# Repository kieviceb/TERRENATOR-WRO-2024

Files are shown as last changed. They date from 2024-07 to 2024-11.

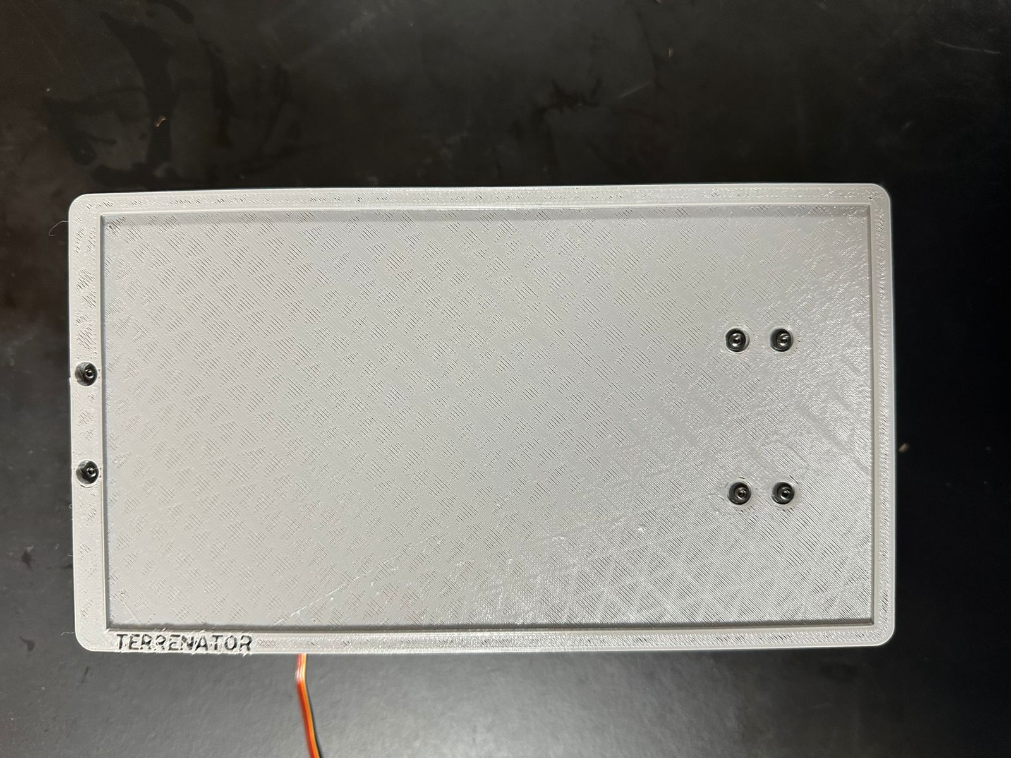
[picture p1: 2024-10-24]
v-photos/WhatsApp Image 2024-10-24 at 6.23.05 AM.jpeg

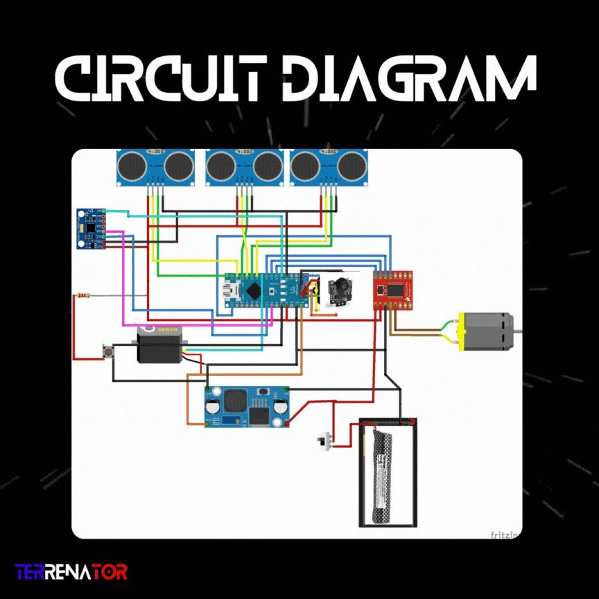
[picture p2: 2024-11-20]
Schemes/Circuit Diagram.jpg

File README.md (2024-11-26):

# Terrenator's readme Bandera de Panamá
TERRENATOR (30 x 18 cm) (25 x 6 cm) (1)



                
This is the official repository of the TERRENATOR team, which is representing Panama in the World Robotics Olympics (WRO) 2024 to be held this year in Izmir, Türkiye. We chose to participate in the category of Future Engineers this year winning first place in the national robotics olympics in our country. In this repository you can find everything related to the development of our robot.

---

## Team members 👨‍💻

Imagen 1

 ## David Rico:
 ### Age: 17

 Imagen 1
 
 David is someone who always tries to solve and constantly seeks the union in the team, he likes sports specifically baseball and likes anime and likes to win.

His role in the team is to design the chassis and 3d parts of the robot, also the circuit and all the components of the robot as well as programming.

## Ericka Ceballos:
### Age: 17

Imagen 1

She is very determined and strong, she is always very tidy and organized and above all she doesn't like to lose, ericka likes programming especially in python, she also likes to socialize a lot, as she is the sociable member of the team.

Her role in the team is the programming of the robot, as well as documenting the whole process of the robot.

## Jean Paul Sosa:
### Age: 17

 Imagen 1

He is the quietest of the team, but at the same time he always likes to be neutral in everything, he is someone that you will hardly make him angry, he is a quiet, chill guy. He loves music and enjoys listening to rock and playing instruments like the guitar, bass and saxo, as well as robotics.

His role in the team is to do some of the robot programming as well as help with the circuitry and documenting everything on the robot.

<br>
 <br>

 > [!NOTE]
> To see the funny photo [here](https://github.com/kieviceb/TERRENATOR-WRO-2024/tree/main/t-photos)

<br>

## Overview of our repository 📜
* `schemes`- contains the circuit diagram.
* `models` - includes all the 3d printed parts of the robot that will go to the international.
* `old models` - includes all the 3d printed parts of the robot that wins in Panama.
* `others`-  This is for other files which can be used to understand the making of the vehicle. 
* `src` - the codes for both challenges, with and without obstacles.
* `t-photos` - photos of the team one formal and a funny one.
* `v-photos` - photos of every angle of the robot, including our previuos version .
* `video` - the link to our youtube channel where you can see our robot in action completing both challenges.
* `README.md` - Here's all our journey in the development of our robot here we explain every part of the robot making.

## Components 🧱
A list of all the electrical and mechanical components in the robot.

|  |  |  | 
| :---: |:---:| :---:|
|[Arduino NANO A000005 x1](https://store-usa.arduino.cc/products/arduino-nano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)|[MPU6050 Gyroscope x1](https://a.co/d/42jYlB6)|[Step down LM2596 x1](https://a.co/d/e4jJKCS)|
|  |  |  |
| [Double Sided Prototype Universal PCB Board x2](https://a.co/d/9mUTqVe) |[TB6612 motor driver](https://a.co/d/fpJSHg1)|[HC-SRO4 ultrasonic sensor x3](https://a.co/d/et6RN4v) |
|  ||  |
|[POLOLU Metal Gearmotor 25Dx65L mm MP 12V with 48 CPR Encoder x1](https://www.pololu.com/product/4863)|[INJORA 7KG 2065 micro servo motor x1](https://a.co/d/3OIRFif)|[Tosiicop Airsoft Lipo Battery 11.1V x1](https://a.co/d/4mkS5gP)|
|  |  |  |
|[Pixy cam v2.1 x1](https://a.co/d/hyOCC5F) |[Electrolytic Capacitor x2](https://a.co/d/2Hp40r2)|[Rocker switch x1](https://a.co/d/dZaNOAK) |
|  |  |  |
|[10K ohm Resistor x1](https://a.co/d/g2p8k1C) |[UTP cable CAT6 ](https://a.co/d/9NCzytp)|[Push button x1](https://a.co/d/8YSMDxr) |
|  |  |  |
|[Fuse Holder Inline screw type x1](https://a.co/d/7VGbSVK) |[Jumper wires x12 ](https://a.co/d/0rLEQiV)|[Ceramic capacitor x3](https://amzn.eu/d/0qPpxa0) |

## Introduction 🎓

- To make all the structure of the robot, it took a lot of time and investigation, we decided to build our robot totally by our selves, the robot's body was make in [OnShape](https://www.onshape.com/en/) Platform , all the design of the robot and all the models and pieces can be found here in `models`, it is compound by 17 parts assembled together. We have passed by a lot of prototypes, at first heavier and bigger, but for turkiye prototype, to make it more light, more smaller, more efficient, we are looking to make the things simple, to make the most efficient autonomous vehicle, we decided to use [Arduino Nano](https://store.arduino.cc/products/arduino-nano) , because it's smaller and has everything that we need to control our robot, we have use a various types of Arduino nano, Like the [Arduino Nano ESP32](https://store.arduino.cc/products/nano-esp32), [Arduino Nano Every](https://store.arduino.cc/products/arduino-nano-every), [Arduino Nano Every](https://store.arduino.cc/products/arduino-nano-every). The reason of why we have used various types of arduino nano, is because every one of them give different capacities, and sometimes we need different capacities in our robot. To understand the making and the programming of the robot please check all the parts of this `README.md`.

## Vehicle Photos 📸

| Front | Right | Back |
|:---:|:---:|:---:|
| front |front |  front |
| Left | Top | Bottom |
|front| front | front|

<br>
 <br>

 > [!NOTE]
>These photos are of the vehicle that will travel to Turkiye to participate in WRO 2024, to see the photos of the car that won the robotics olympics in Panama you can go to the photos folder of the vehicle by clicking [here](https://github.com/kieviceb/TERRENATOR-WRO-2024/tree/main/v-photos)

<br>

---

## Circuit Diagram

<p align="center">
  Imagen 1
</p>

This circuit diagram represents the connections of a robotic system powered by a battery pack and controlled by an Arduino Nano. It integrates three ultrasonic sensors for obstacle detection, a servo motor for steering, and a DC motor for torque and speed via a TB6612 motor driver module. The MPU6050 sensor provides orientation data (gyroscope and accelerometer), likely used for navigation adjustments. A Pixy Cam is included for visual object tracking. Connections include multiple power and ground lines to ensure stable operation, while the battery supplies energy to the motors and sensors. UTP wires link the Arduino to the motor driver, servo, and sensors, ensuring precise control and data flow.

<br>
 <br>

 > [!NOTE]
> To a more detailed explanation go to the schemes readme by clicking [here](https://github.com/kieviceb/TERRENATOR-WRO-2024/tree/main/Schemes)

<br>

---

## Mobility Strategy 🚲

### 1- Movement

- Motor: Our  gearmotor consists of a medium-power, 12 V brushed DC motor combined with a 20.4:1 metal spur gearbox, and it has an integrated 48 CPR quadrature encoder on the motor shaft, which provides 979.62 counts per revolution of the gearbox’s output shaft. The gearmotor is cylindrical, with a diameter just under 25 mm, and the D-shaped output shaft is 4 mm in diameter and extends 12.5 mm from the face plate of the gearbox, you can find our motor [here](https://www.pololu.com/product/4863).

<p align="center">
  Imagen 1
</p>

We used a 3D printed traction system in the back axle of the car, is specifically designed to enhance performance and maneuverability. This system involves a set of precisely engineered gears that provide consistent and reliable power transfer from the motor to the rear wheels. The gear configuration ensures that torque is effectively distributed, enabling the car to maintain traction even during rapid acceleration. It provides the power, control, and reliability needed for the commpetition.

### 2- Steering
 
- Steering: The steering is handled by a servomotor, during this project we discovered that using a plastic gear servo is not a good choice, because of the speed of the robot, it tends to break easily inside; thats how we ended up using at first a MG995 servo which is metal gear so it doesnt break so easily, finally for the last prototype to reduce weight and size we found a micro metal gear servo (INJORA 7KG 2065 micro servo motor) , with the power of the big one but weighting less and smaller. Having the steering on the front axle, in vertical position to make movement with more precission.  

<p align="center">
  Imagen 1
  Imagen 2
</p>

### 3- Sensors

- [HC-SR04](https://www.sparkfun.com/products/15569):
The HC-SR04 is a distance sensor that uses ultrasound to determine the distance of an object in a range of 2 to 450 cm. It is notable for its small size, low power consumption and good accuracy. The HC-SR04 sensor is the most widely used ultrasonic sensor, mainly due to the amount of information and projects available on the web. It is also the most used in robotics projects such as maze or sumo robots, and in automation projects such as level or distance measurement systems.

This sensor provides 2cm to 400cm of non-contact measurement functionality with a ranging accuracy that can reach up to 3mm. Each HC-SR04 module includes an ultrasonic transmitter, a receiver and a control circuit.

<p align="center">
  Imagen 1
</p>

-How the HC-SR04 Ultrasonic Distance Sensor Works?
It emits an ultrasound at 40 000 Hz which travels through the air and if there is an object or obstacle on its path It will bounce back to the module. Considering the travel time and the speed of the sound you can calculate the distance.

<p align="center">
AJAJ
</p>

In order to generate the ultrasound we need to set the Trig pin on a High State for 10 µs. That will send out an 8 cycle ultrasonic burst which will travel at the speed of sound. The Echo pins goes high right away after that 8 cycle ultrasonic burst is sent, and it starts listening or waiting for that wave to be reflected from an object.

To detect the walls with the HC-SR04 it took us a lot of time to figure out a way of using the ultrasonic sensors to avoid the walls successfully, in our previous prototype we had all the sensors horizontally and it gave us good lectures most of the time, but not always, thats why investigating a little further and using trigonometry we found out that the position of the ultrasonic sensors on the sides vertically is way more effective and the main reason we were having trouble at the curves; What was happening was that the TX and RX sides, when reaching the curves, one was further ahead than the other and the pulse did not reach the same place and was sending out erroneous data, therefore when placing them vertically this does not happen, both pulses collide equally, and the signal bounces back uniformly, sending out useful data.

<p align="center">
Imagen 1
</p> 

In addition to this, as can be seen in the photos of the vehicle, our ultrasonic sensors each have a Ceramic capacitor, and before explaining why we have it we should know what it is. A ceramic capacitor is a fixed-value capacitor where the ceramic material acts as the dielectric. It is formed by two or more alternating layers of ceramic and a metallic layer that acts as the electrode. The composition of the ceramic material defines the electrical behavior and therefore the applications.

Knowing this, our intention in placing these ceramic lentils or capacitors is to be able to soften the signals of the ultrasonic sensors, so to speak, filter the signals; this helped to not protrude peaks in the sound waves transmitted by the ultrasonic sensor and so that all data are received with the greatest possible clarity.

<p align="center">
Imagen 1
</p> 

- [MPU-6050](https://invensense.tdk.com/products/motion-tracking/6-axis/mpu-6050/):
MPU6050 sensor module is complete 6-axis Motion Tracking Device. It combines 3-axis Gyroscope, 3-axis Accelerometer and Digital Motion Processor all in small package. Also, it has additional feature of on-chip Temperature sensor. It has I2C bus interface to communicate with the microcontrollers. It has Auxiliary I2C bus to communicate with other sensor devices like 3-axis Magnetometer, Pressure sensor etc. If 3-axis Magnetometer is connected to auxiliary I2C bus, then MPU6050 can provide complete 9-axis Motion Fusion output.
<p align="center">
Imagen 1
</p> 

- Orientation and polarity of the axes and rotations of the MPU-6050:
It is a 6-axis motion sensor that measures linear accelerations and angular velocities. It uses a three-dimensional coordinate system with axes labeled +X, +Y and +Z, representing forward/backward, left/right and up/down directions, respectively. The +X axis points to the right, +Y points up and +Z points vertically away from the top surface of the sensor, with their negative counterparts in the opposite directions. Rotational motions are measured around these axes, with positive rotation defined by the right-hand rule: if the fingers of the right hand are bent in the direction of rotation, the thumb points along the positive axis. For example, clockwise rotation around the +X (roll), +Y (pitch) or +Z (yaw) axes is considered positive, while counterclockwise rotation is negative. This configuration allows the MPU-6050 to track motion in 3D, making it essential for applications such as balancing robots, drones or any system that requires accurate tracking of motion and orientation.
<p align="center">
Imagen 1
</p> 
For our vehicle, we are only interested in the z-axis (Yaw) of the MPU-6050, because this axis is the one that will allow us to determine the desired angles for our robot to work, in our vehicle, we have to let the sensor calibrate to start, at the time of being calibrated the angles that we are interested in are those of 90 degrees to be able to make a right angle turn and to help stabilize the PD, we had an issue that in the straight lines the PD is well stabilized, but when making the curves it went crazy, and began to oscillate a lot, then to have more precise turns, We used the Z axis (Yaw) of the MPU-6050, but this also had its complications, because the values sent by the z axis were not so simple for the robot to understand, because the first curve, if they were 90 degrees, but the next curve for example the gyroscope threw 180 degrees, and it is logical, but it was more difficult to implement, so we thought of several possible solutions for this, we thought of resetting the values of Yaw or the z-axis after each curve, so that if in the serial we can always see that it turns 90 degrees exactly, this greatly affected the accuracy of the sensor.

 <br>
 <br>

 > [!NOTE]
>In order to see the coding of each motion component or sensor explained, please go to the coding part for further understanding, as well as you can always review the vehicle circuit diagram and review the component list, and also you can check our youtube channel. [Here](https://www.youtube.com/@TERRENATORTEAM)

<br>
In this way, in the vehicle, the MPU-6050 works using the desired angles through functions so that the robot can make precise turns. I will go into much more detail about this in the code section.

### 4- [MPU-6050 LIBRARIES](https://invensense.tdk.com/products/motion-tracking/6-axis/mpu-6050/):

 First of all we need to initialize our MPU-6050 We need to declare all the variables for it, and it has some specific libraries that you can find it here:

https://github.com/jrowberg/i2cdevlib
https://github.com/ZHomeSlice/Simple_MPU6050
https://github.com/ZHomeSlice/Simple_Wire

And if you don't know how to install it, you need to watch this video, (it's in spanish):

- [MPU-6050  Youtube](https://www.youtube.com/watch?v=TwFZ4BJUX5c&t=1805s)

But i´ll explain here:
First we need to donwload the I2C Library that will make easy the 12c conection with the arduino nano, this library it´s of free software and multiplatform, and this library complement the wire library with the arduino IDE, so, we need to goon the first link i put here and [here](https://github.com/jrowberg/i2cdevlib) then, in the part of code, the green part on the git hub, we will donwnload the zip, so once it is installed we need to extract the file, once it is extracted, we need to go to the 12cdevlib master folder, then the arduino folder, here are a lot of libraries we can use for different proyects, so here we have to search the 12cdev folder, once we find it we have to select it an copy it, so once we do this we have to go to arduino folder, in most of cases it is set default on document, once there we go to libraries and then we paste 12cdev there.

That was our first library, now we need to download the [Simple_MPU6050](https://github.com/ZHomeSlice/Simple_MPU6050)  library, wich this is most simple to use, so we have to intall the zip of this library, and then in the arduino IDE we have to include the library there, in other words we have to add the zip file to his library inside the IDE.

Even in this part you might have some problems to initialize and use the code, that´s because in the video they dont say this but we need another library, that is for comunication, espacifically the [Simple_Wire](https://github.com/ZHomeSlice/Simple_Wire), to install it you have to follow the same steps of the second library.

Once we have all the libraries needed, we are ready to use the MPU-6050.

### 4- Camera

- 5-[PIXY CAM 2.1](https://pixycam.com/2021/05/20/introducing-pixy-2-1/):
The PixyCam 2.1 is a fast and versatile vision sensor for DIY robotics, offering significant improvements over its predecessor. Its horizontal field-of-view has been expanded to 80 degrees, allowing it to capture more of the environment in each frame, albeit with minor spherical distortion. The camera features a replaceable M12 lens mount with adjustable focus, enabling it to focus on objects as close as 0.25 inches. It also minimizes chromatic distortion at the edges and boasts an F-stop of 2.0, improving light gathering and reducing pixel noise, resulting in higher detection accuracy. Capable of processing images at 60 frames per second, it updates object positions every 16.7 milliseconds, making it ideal for tracking fast-moving objects or precise line-following. The Color Connected Components (CCC) algorithm allows to detect objects based on hue and saturation, remaining robust under varying lighting conditions. It supports up to 7 color signatures or numerous objects using color codes. While retaining the software, firmware, and features of PixyCam 2, this version is slightly larger but significantly more efficient for detection and tracking tasks.
---
<p align="center">
  Imagen 1
  Imagen 2
</p>

<br>
 <br>
 
---

 > [!NOTE]
>In the case of our pixy cam 2.1, we always need to calibrate our camera before the competition in the track of the event, this because as it has happened to us before we always need to check that the pixy cam recognizes well the blocks and the color lines, because it happens that the illumination affects the block detection of the pixy cam, then we always need to enter the track with our laptop using specifically the pixymon program, to be able to know that the signatures are being detected effectively, to calibrate our pixy cam we need to use a microUSB cable connected to the laptop to open the pixymon, pixymon is to check the view of the camera.

<br>

## Chasis & 3D Parts

In the chassis and 3D part, you can find all the 3D parts that made up the robot that won in Panama in the old models part.

So the chassis and the design of the car going to Turkey took a long time because our ideas; to make the robot of the national competition much smaller, agile, faster and prettier, we had to make a completely new chassis, in this one changing several parts of the assembly, for example in the steering system, since in our previous robot, the steering system was based on moving a cylinder with teeth that moved a stripped line that gave direction to the robot, the problem with this steering design was that its a bit imprecise so, we adopted a steering design similar to the Ackerman steering, and we also changed the servo motor.

---
<p align="center">
  Imagen 1
  Imagen 2
</p>
---

Then for the traction, we have four parts, the big gear for motor that this is the gear that give us the torque to move the robot, we have a game of gears that we can modify in case we need speed or more torque, and we have a fixed drive motor retainer, here we have a support for the motor, and we have the small gear for the drive axle, and we have the traction support.

---
<p align="center">
  Imagen 1
  Imagen 2
</p>

---
Then we have the skeleton: 
Here in the skeleton is the main base chasis of the robot, here we can find in the physical one the motor game with his gears, the servo motor, and the modifications that make the steering have better movements.

And also here we have the main shell, here we can find all that makes our robot, here are all the circuits for the robot and the base for the camera.

---
<p align="center">
  Imagen 1
  Imagen 2
</p>

---

Now for the sensors, we have made a lot of support for them, but with this one we made the correct one, it is more outside beacuase they give us better data in this way.

---

<p align="center">
  Imagen 1
</p>

---

Now with the wheels, we have designed it by ourself, because in that way we can ajust everything we want and it's so much better in that way. For the traction wheels they are a little bit bigger.

---
<p align="center">
  Imagen 1
  Imagen 1
</p>

<br>
 <br>

 > [!NOTE]
> All this can be find in the main [README](https://github.com/kieviceb/TERRENATOR-WRO-2024/blob/main/README.md) And very important you can see a tutorial video of all the structure of the robot by clicking [here](https://www.youtube.com/@TERRENATORTEAM)

<br>

## Code & programming
In this section, we will proceed to explain the codes of the open and obstacle challenge, the codes will be explained SEQUENTIALLY in the SRC folder, there you will have a more general explanation of the code, in this part of the readme we will break down the code of each component that integrates the code, to have a much clearer and understandable epxlicacion each part of the code. Before going to explain each code of the respective round, there will be a list to know the order in which each part of the code will be explained, and remember to see the sequential explanation, it is in the SRC folder.

## Open Challenge Code:

### 1. **Library Imports**

```ino
#include <Servo.h>
#include "Simple_MPU6050.h"
#include <Wire.h>
```
- **Servo.h**: Used to control a servo motor.
- **Simple_MPU6050.h**: Library for interfacing with the MPU6050 sensor (used for orientation).
- **Wire.h**: Library for I2C communication, necessary for interacting with the MPU6050.

---

### 2. **MPU6050 Configuration**
```ino
#define MPU6050_ADDRESS_AD0_LOW     0x68   // I2C address when AD0 pin is LOW
#define MPU6050_ADDRESS_AD0_HIGH    0x69   // I2C address when AD0 pin is HIGH
#define MPU6050_DEFAULT_ADDRESS     MPU6050_ADDRESS_AD0_LOW  // Default I2C address for the MPU6050

Simple_MPU6050 mpu;  // Create an instance of the MPU6050 object
float yawActual = 0;  // Global variable to store the current Yaw (rotation around the Z-axis)
float yawInicial = 0; // Initial yaw value for reference
```
- Defines the I2C addresses for the MPU6050 sensor, depending on the state of the AD0 pin.
- Initializes the `Simple_MPU6050` object for reading data from the sensor.
- `yawActual` holds the current yaw angle (rotation around the Z-axis).
- `yawInicial` stores the initial yaw value, often used for calculating differences in orientation.

---

### 3. **Servo configuration**
```ino
Servo servoDireccion;  // Servo object to control the steering
int pinServo = 6;      // Pin to which the servo is connected
int anguloIzquierda = 87;  // Angle for left turn
int anguloCentro = 90;      // Angle for straight position (centered)
int anguloDerecha = 105;    // Angle for right turn
int anguloMPU = 0;         // Angle value derived from MPU data
```
Initializes the servo and assigns specific angles for left, center, and right turns; also a derivated angle from the mpu6050.

### 4. **PD Control (Proportional-Derivative Control) Variables**
Before we explain the coding of this, we need to explain what is it:

PD Control (Proportional-Derivative) is a technique in control theory used to adjust the behavior of a system based on:

-The current error (Proportional): How much the system deviates from the desired value at this moment.
-The rate of change of the error (Derivative): How quickly the error is changing over time.

A PD controller is a simplified form of the PID control, omitting the Integral term. It is useful when:

-Accumulated errors (integral term) do not need to be eliminated.
-The system requires fast and stable responses.

Mathematical Function of PD
The output of the controller (referred to as adjustment or correction) is calculated as:
null-109

where Kp is the proportional gain, Kd the derivative gain, the error the difference between the desired value (setpoint) and the current system value and and d multiplied by the error between d its the Derivative of the error, i.e., the rate of change of the error over time.

-Implementation of PD Control in the code:
The code uses a PD controller to dynamically adjust the servo motor angle based on error. Below, I break down each step of its implementation:

float Kp = 2.0;: Defines the proportional gain.

A higher value means that the system responds more aggressively to error.
Too high a value can make the system unstable (oscillate).
float Kd = 1.0;: Defines the derivative gain.

Helps to smooth the system response. If the error is changing rapidly, this term reduces the setting to avoid oscillations.
float lastError = 0;: Variable to store the error of the previous iteration.
```ino
float Kp = 0.63;  // Proportional gain for PD control
float Kd = 0.4;   // Derivative gain for PD control
float alpha = 0.15;  // Smoothing factor for yaw
float lastError = 0; // Stores the last error value for derivative calculation
int curva = 0;      // Counter for curves detected by the robot
const int botonPin = A7;  // Button pin used to start/stop the robot
bool enMarcha = false;    // Robot's state: false = stopped, true = running
```
- **PD control constants** (`Kp` and `Kd`): Used to tune the proportional and derivative responses of the control loop.
- **Yaw smoothing** (`alpha`): A factor used to smooth the yaw (orientation) readings from the MPU6050 to avoid abrupt changes.
- **Button and robot state**: The button on pin `A7` is used to start or stop the robot. `enMarcha` indicates whether the robot is running or stopped.

---

### 5. **Ultrasonic Sensor and MotorPin Setup**

```ino
int trigIzquierdo = 9, echoIzquierdo = 10;  // Left sensor pins
int trigCentro = 15, echoCentro = 14;        // Center sensor pins
int trigDerecho = 7, echoDerecho = 8;        // Right sensor pins

int motorPin1 = 5, motorPin2 = 4, enablePin = 3, standbyPin = 16;  // Motor pins for control
```
- Defines the pins for the three ultrasonic sensors (left, center, right). These are used to detect obstacles.
- Motor control pins: These pins are used to control the motors (direction, enable, and standby).

---

### 6. **Time Control and Blocking Variables**

```ino
unsigned long tiempoUltimaCurva = 0;
const long bloqueoTiempo = 2000;  // Time between turns to avoid continuous turning
int bloqueadorI = 65;  // Blocking threshold for left sensor
int bloqueadorD = 65;  // Blocking threshold for right sensor
```
- `tiempoUltimaCurva`: Stores the last time a curve was detected to prevent rapid consecutive curve turns.
- `bloqueoTiempo`: Time interval (in milliseconds) that defines how often the robot can turn to avoid constant turns.
- `bloqueadorI` and `bloqueadorD`: Thresholds for the left and right sensors to prevent false readings from triggering unnecessary turns.

---

### 7. **MPU6050 Data Processing Function**

```ino
void procesarMPU(int16_t *gyro, int16_t *accel, int32_t *quat, uint32_t *timestamp) {
    Quaternion q;  // Quaternion object to store rotation data
    VectorFloat gravity;  // Gravity vector for accurate yaw calculation
    float ypr[3] = { 0, 0, 0 };  // Yaw, pitch, roll values
    float xyz[3] = { 0, 0, 0 };  // Raw sensor data values

    // Get quaternion, gravity, and yaw-pitch-roll data from the MPU
    mpu.GetQuaternion(&q, quat);
    mpu.GetGravity(&gravity, &q);
    mpu.GetYawPitchRoll(ypr, &q, &gravity);
    mpu.ConvertToDegrees(ypr, xyz);

    // Update the yaw value globally
    yawActual = (int)xyz[0];
}
```
- **`procesarMPU`**: This function processes the MPU6050 data (gyroscope, accelerometer) to extract yaw, pitch, and roll values using quaternions and gravity data. The yaw value (`yawActual`) is updated globally.

---

### 8. **PD Control Initialization**

```ino
void inicializarControlPD() {
    servoDireccion.attach(pinServo);  // Attach the servo to the pin
    //servoDireccion.write(anguloCentro); // Optional: Set the servo to the center position (straight)
}
```
- **`inicializarControlPD`**: Initializes the PD control by attaching the servo to the specified pin and optionally setting it to the center position.

---

### 9. **Servo Control Function**

```ino
void move_steer(int pos) {
    int currentPos = servoDireccion.read();  // Get the current position of the servo
    if (pos > currentPos) {
        // Move the servo to the right (gradually increasing position)
        for (int i = currentPos; i <= pos; i++) {
            servoDireccion.write(i);
            delay(10);  // Small delay to smooth the movement
        }
    } else {
        // Move the servo to the left (gradually decreasing position)
        for (int i = currentPos; i >= pos; i--) {
            servoDireccion.write(i);
            delay(10);  // Small delay to smooth the movement
        }
    }
}
```
- **`move_steer`**: This function smoothly moves the servo to a target position (`pos`). It adjusts the servo's position incrementally (with small delays) to avoid abrupt movements.

### 10. **PD Control Adjustment Function**

```ino
void ajustarAngulo(float error, int anguloDeseado) {
    float derivada = error - lastError;  // Calculate the derivative term (rate of change of error)
    float ajuste = (Kp * error) + (Kd * derivada);  // PD control formula
    lastError = error;  // Update the last error value for the next iteration

    anguloDeseado += ajuste;  // Apply the adjustment to the desired angle
    anguloDeseado = constrain(anguloDeseado, anguloIzquierda, anguloDerecha);  // Constrain the angle to avoid exceeding limits
    move_steer(anguloDeseado);  // Move the servo to the adjusted angle
}
```
- **`ajustarAngulo`**: This function adjusts the steering angle based on the error (difference between desired and actual angles) using the PD control formula. It ensures the angle stays within limits (`anguloIzquierda` and `anguloDerecha`) and moves the servo accordingly.

---
### 11. **Ultrasonic Sensor Distance Measurement**

```ino
long medirDistancia(int trigPin, int echoPin) {
    // Trigger the ultrasonic sensor
    digitalWrite(trigPin, LOW);  // Start with LOW to ensure a clean pulse
    delayMicroseconds(3);
    digitalWrite(trigPin, HIGH);  // Send a HIGH pulse to trigger the sensor
    delayMicroseconds(10);
    digitalWrite(trigPin, LOW);  // End the pulse

    // Measure the duration of the echo pulse
    long duracion = pulseIn(echoPin, HIGH);  // Get the duration of the echo signal
    return duracion * 0.034 / 2;  // Convert the duration into distance (in cm)
}
```
- **`medirDistancia`**: This function triggers the ultrasonic sensor and calculates the distance based on the time it takes for the echo to return.

---

### 12. **Function: `calcularAnguloObjetivoI(int curva)`**

```ino
int calcularAnguloObjetivoI(int curva) {
    if (curva % 4 == 1) return -70;     // Curvas 1, 5, 9, ...
    else if (curva % 4 == 2) return -160; // Curvas 2, 6, 10, ...
    else if (curva % 4 == 3) return 110;   // Curvas 3, 7, 11, ...
    else return 20;                      // Curvas 4, 8, 12, ...
}
```

This function calculates the target angle for the servo motor (or steering mechanism) based on the curve number. The variable `curva` represents the current curve number.
- The function uses the modulo operator (`%`) to determine the remainder when dividing `curva` by 4. This helps categorize the curve into one of four possible cases (1 through 4).
- Based on the result of the modulo operation, the function returns a specific angle for the servo.
Here’s how the curve number determines the angle:
- **When `curva % 4 == 1`** (i.e., curves 1, 5, 9, ...): The servo will turn to **-70°**.
- **When `curva % 4 == 2`** (i.e., curves 2, 6, 10, ...): The servo will turn to **-160°**.
- **When `curva % 4 == 3`** (i.e., curves 3, 7, 11, ...): The servo will turn to **110°**.
- **When `curva % 4 == 0`** (i.e., curves 4, 8, 12, ...): The servo will turn to **20°**.

### 13. **Function: `calcularAnguloObjetivoD(int curva)`**

```ino
int calcularAnguloObjetivoD(int curva) {
    if (curva % 4 == 1) return 75;     // Curvas 1, 5, 9, ...
    else if (curva % 4 == 2) return 155; // Curvas 2, 6, 10, ...
    else if (curva % 4 == 3) return -105;   // Curvas 3, 7, 11, ...
    else return -15;                      // Curvas 4, 8, 12, ...
}
```
This function also calculates the target angle for the servo motor based on the curve number. The input `curva` represents the current curve number.
Similar to the previous function, the modulo operator (`%`) is used to categorize the curve number, and the function returns a specific angle based on that categorization.
Here’s how the curve number determines the angle:
- **When `curva % 4 == 1`** (i.e., curves 1, 5, 9, ...): The servo will turn to **75°**.
- **When `curva % 4 == 2`** (i.e., curves 2, 6, 10, ...): The servo will turn to **155°**.
- **When `curva % 4 == 3`** (i.e., curves 3, 7, 11, ...): The servo will turn to **-105°**.
- **When `curva % 4 == 0`** (i.e., curves 4, 8, 12, ...): The servo will turn to **-15°**.
  
### 14. **Motor control**
Then we will enter the Void functions, which are functions that in determinod time we can call for certain event that we need to occur, in this case the movement of the car, the motorpin 1 in HIGH and motorpin 2 in low makes the motor advance, in case of putting this configuration backwards would make the car go in reverse, and also atravz of the PWM can adjust the speed of the motor, as we can see:
```ino
void avanzar(int velocidad) {
    // Set the motor to rotate in a specific direction.
    digitalWrite(motorPin1, HIGH); // Set motorPin1 to HIGH to define the forward rotation direction.
    digitalWrite(motorPin2, LOW);  // Set motorPin2 to LOW to ensure the motor rotates in the desired direction.
    // Control the motor's speed using PWM (Pulse Width Modulation).
    analogWrite(enablePin, velocidad); // Generate a PWM signal on enablePin to adjust the motor speed (range: 0-255).
}

```
Now we will have the function to stop the motor, that would be with the two pins in LOW, in the code it would be like this:
```ino
void detener() {
    // Stop the motor by cutting power to both motor direction pins.
    digitalWrite(motorPin1, LOW); // Set motorPin1 to LOW to stop the motor.
    digitalWrite(motorPin2, LOW); // Set motorPin2 to LOW to ensure no rotation.

    // Set the speed to zero to fully disable the motor.
    analogWrite(enablePin, 0); // Generate a PWM signal of 0 to turn off the motor.
}
```

### 15. **Function: `detectarCurva(long distanciaIzquierda, long distanciaCentro, long distanciaDerecha)`**
This function is responsible for detecting curves on the path and adjusting the robot's movements to navigate those curves. It uses data from distance sensors (left, center, and right) and a gyroscope to determine the robot's orientation and make real-time adjustments. Below is a step-by-step breakdown of how the function works:
**Input Parameters**:
   - `distanciaIzquierda`: Distance measured by the left sensor.
   - `distanciaCentro`: Distance measured by the center sensor.
   - `distanciaDerecha`: Distance measured by the right sensor.
**Calculating the Error and Sum**:
   - **Error Calculation**:
     ```ino
     float error = distanciaIzquierda - distanciaDerecha;
     ```
     This computes the difference between the distances measured by the left and right sensors. This difference (`error`) indicates whether the robot is closer to the left or right side. A positive error suggests the left sensor detects a closer object, and a negative error suggests the right sensor detects a closer object.

   - **Sum Calculation**:
     ```ino
     float sum = distanciaIzquierda + distanciaDerecha;
     ```
     The sum of the left and right distances gives an overall sense of the space around the robot, used to assess whether there is enough open space to proceed.

   - **Storing Last Error**:
     ```cpp
     lastError = error;
     ```
     The current error is stored for later use (possibly for debugging or future calculations).
**Time Check for Curve Blocking**:
   - **Time Since Last Curve**:
     ```cpp
     unsigned long tiempoActual = millis(); 
     if (tiempoActual - tiempoUltimaCurva >= bloqueoTiempo)
     ```
     This checks whether enough time has passed since the last detected curve (`tiempoUltimaCurva`). The purpose of this is to prevent the robot from continuously detecting curves or making unnecessary turns too quickly. If the time difference exceeds `bloqueoTiempo`, the robot is allowed to detect and adjust to another curve.
**Curve Detection and Navigation**:
   - **Left Turn Detection**:
     ```cpp
     if (error > 1 && distanciaCentro < 58 && sum > 90 && distanciaIzquierda > bloqueadorI) {
     ```
     This condition checks if the robot should turn left:
     - If `error > 1`, it suggests the left side is closer, indicating the need to turn left.
     - If `distanciaCentro < 58`, the center sensor detects something close, indicating the robot is navigating near an obstacle or a curve.
     - If `sum > 90`, the combined distance on the left and right sides suggests there’s enough room for a curve.
     - If `distanciaIzquierda > bloqueadorI`, the robot ensures it’s not too close to the left obstacle.
     
     If all these conditions are met, the robot recognizes a left curve and proceeds with the turn:
     - **Increment Curve Counter**: 
       ```cpp
       curva++;
       ```
       The `curva` counter is incremented to keep track of how many curves the robot has encountered.
     - **Calculate Target Angle for Left Turn**: 
       ```cpp
       int anguloObjetivo = calcularAnguloObjetivoI(curva);
       ```
       The function `calcularAnguloObjetivoI()` determines the target angle for the robot to turn to navigate the curve, based on the curve count (`curva`).
     - **Perform the Turn**: 
       ```cpp
       while (abs(yawActual - anguloObjetivo) > 2) {
           servoDireccion.write(119);  // Turn left
           avanzar(250);  // Move forward while turning
       }
       ```
       The robot keeps turning left (by controlling the servo direction) until the current yaw angle (`yawActual`) reaches the target angle (`anguloObjetivo`). A tolerance of 2 degrees is allowed.
     - **Stop Turning and Return to Center**:
       ```cpp
       servoDireccion.write(anguloCentro);
       delay(100);  // Short delay to stabilize
       tiempoUltimaCurva = tiempoActual;  // Update last curve time
       bloqueadorD = 1500;  // Block right turns temporarily
       ```
       After completing the left turn, the robot’s servo is reset to the center, and a brief delay is added to stabilize. It also updates the time of the last curve and blocks right turns temporarily with `bloqueadorD`.

   - **Right Turn Detection**:
     ```cpp
     else if (error < -1 && distanciaCentro < 58 && sum > 90 && distanciaDerecha > bloqueadorD) {
     ```
     Similar to the left turn detection, but this condition checks if the robot should turn right:
     - If `error < -1`, it suggests the right side is closer, indicating a need to turn right.
     - If `distanciaDerecha > bloqueadorD`, the robot ensures it’s not too close to the right obstacle.

     The steps for a right turn are almost identical to the left turn, with a few changes:
     - The target angle for the right turn is calculated using `calcularAnguloObjetivoD(curva)`.
     - The robot turns right by writing to the servo with `servoDireccion.write(69)`.

   - **If No Curve is Detected**:
     ```cpp
     else {
         ajustarAngulo(error, anguloCentro);
         avanzar(200);  // Move forward normally
     }
     ```
     If no curve is detected (i.e., neither left nor right conditions are met), the robot simply adjusts its angle to stay centered (`ajustarAngulo()`) and continues moving forward.

**Final else Block**:
If the time since the last curve is not enough (`tiempoActual - tiempoUltimaCurva < bloqueoTiempo`), the robot will again adjust its angle and move forward normally:
```cpp
else {
    ajustarAngulo(error, anguloCentro);
    avanzar(200);  // Move forward normally
}
```
This function helps the robot navigate curves effectively by constantly adjusting its heading and movement based on real-time sensor data.

### 16. **Function: `actualizar()`**
This function updates the sensor readings, checks for curves, and provides debug output on the serial monitor.
```ino
void actualizar() {
    // Measure distances from the left, center, and right sensors
    long distanciaIzquierda = medirDistancia(trigIzquierdo, echoIzquierdo);
    long distanciaCentro = medirDistancia(trigCentro, echoCentro);
    long distanciaDerecha = medirDistancia(trigDerecho, echoDerecho);

    // Call the function to detect a curve based on sensor data
    detectarCurva(distanciaIzquierda, distanciaCentro, distanciaDerecha);

    // If 12 curves have been detected, stop the robot and pause for 60 seconds
    if (curva == 12) {
        servoDireccion.write(90);  // Center the servo
        avanzar(250);  // Move forward briefly
        delay(700);  // Wait for 700 ms
        detener();  // Stop the robot
        delay(60000);  // Wait for 60 seconds
    }

    // Print sensor and robot state data to the serial monitor for debugging
    Serial.print("Yaw: "); Serial.print(yawActual);
    Serial.print(" | Distancia Izquierda: "); Serial.print(distanciaIzquierda);
    Serial.print(" | Distancia Centro: "); Serial.print(distanciaCentro);
    Serial.print(" | Distancia Derecha: "); Serial.print(distanciaDerecha);
    Serial.print(" | Error: "); Serial.println(lastError);
}
```
- **Sensor data**: Reads the distance from the left, center, and right sensors.
- **Curve detection**: Calls the `detectarCurva()` function to check for curves.
- **Robot control**: Stops the robot after 12 curves and pauses for 60 seconds.
- **Debugging output**: Prints useful information (yaw, distances, error) to the serial monitor.
---
### 17. **Function: `setup()`**
This function initializes the robot’s hardware, including sensors, motors, and communication interfaces.
```ino
void setup() {
    Serial.begin(115200);  // Start serial communication at 115200 baud rate
    
    // Initialize sensor pins (left, center, right sensors)
    pinMode(trigIzquierdo, OUTPUT);
    pinMode(echoIzquierdo, INPUT);
    pinMode(trigCentro, OUTPUT);
    pinMode(echoCentro, INPUT);
    pinMode(trigDerecho, OUTPUT);
    pinMode(echoDerecho, INPUT);

    // Initialize motor control pins
    pinMode(motorPin1, OUTPUT);
    pinMode(motorPin2, OUTPUT);
    pinMode(enablePin, OUTPUT);
    pinMode(standbyPin, OUTPUT);
    digitalWrite(standbyPin, HIGH);  // Set standby pin to HIGH to enable motors
    
    // Initialize PD control system
    inicializarControlPD();

    // Initialize MPU6050 (gyroscope/accelerometer)
    Wire.begin();  // Start I2C communication
    Wire.setClock(400000);  // Set I2C clock speed to 400 kHz
    
    Serial.println(F("Iniciando calibración del MPU6050..."));
    mpu.SetAddress(MPU6050_ADDRESS_AD0_LOW)
       .CalibrateMPU()  // Calibrate the MPU6050 sensor
       .load_DMP_Image();  // Load the DMP (Digital Motion Processor) image for data processing
    mpu.on_FIFO(procesarMPU);  // Set up a callback function to process the MPU data from the FIFO buffer
    
    delay(100);  // Wait for the system to stabilize before starting the main loop
}
```

- **Serial communication**: Initializes communication for debugging and monitoring.
- **Sensor pin configuration**: Sets up the pins for the distance sensors.
- **Motor control**: Configures the pins used to control the robot’s motors.
- **MPU6050 sensor setup**: Initializes and calibrates the MPU6050 sensor to track the robot’s orientation.
- **Control system initialization**: Sets up the PD controller for motor and servo control.
---
These functions together enable the robot to detect curves, navigate based on sensor data, and output debug information, while ensuring proper initialization and configuration of the robot's hardware.
### 18. **Main Control Loop**

```ino
void loop() {
    if (!enMarcha) {  // If the robot is NOT running
        if (analogRead(botonPin) == 0) {  // If the button is pressed
            enMarcha = true;                   // Change the state to "running"
            Serial.println("Robot running!");
            servoDireccion.write(anguloCentro);  // Center the servo
        } else {
            detener();  // Keep the robot stopped if the button is not pressed
        }
    } 
    if (enMarcha == true) {  // If the robot is running
        mpu.dmp_read_fifo();  // Read data from the MPU6050 sensor
        actualizar();         // Execute PD control for adjusting the steering
        delay(5);             // Small delay for smooth operation
    }
}
```
- **`loop`**: The main loop that continuously checks if the robot is running. If it is running, the loop reads sensor data, adjusts the steering based on PD control, and moves the robot accordingly. If the button is pressed, the robot starts.
---

### Why do we use PD?:
1- To maintain stability: Avoid abrupt movements or overcorrections that could destabilize the robot.

2- To improve precision: Adjust the steering angle based on real-time data, ensuring that the robot follows the desired path.

3- For smooth motion: Thanks to the derivative term, it reduces oscillations, achieving a smooth ride.

4- For adaptability: Responds dynamically to changes in the environment, such as curves or detours, by adjusting the robot's direction.

---

### Obstacle avoidance strategy
To avoid the obstacles we changed our previous strategy that consisted of dividing the vision of the pixy cam in 9 sections and creating movements according to each function, but we had problems with that since each section had to have two movements, one for each color block, which took up a lot of space and we could not use a single arduino and we decided to use 2 which over time we realized was quite impractical, so, for the international final we created a new strategy, we divided the camera vision but this time we used something like a kind of limit for each color using the X coordinates of the camera; so as you can see in the image, 

Green limit

the limit of the green blocks is on the right side of the camera or in the code the limit "zetaXmin", for the red blocks the limit is on the left side, which we call "deltaXmin", our strategy consists of the limits being what mark the safe zone of each block, so every time it detects a block outside its limit it What it will do is move until the block of its respective color is in its safe zone, the corresponding limit.

---

## Obstacle Challenge Code:

To see the complete code go to the [SRC](https://github.com/kieviceb/TERRENATOR-WRO-2024/tree/main/src) File on the git hub.

---

### 1. Libraries and MPU6050 directions
first we need to include all the libraries that we are gonna use for the second challegne code, here we use **`Servo.h`**, **`Pixy2.h`**, **`Simple_MPU6050.h`**, **`Wire.h`**.

Then we have the MPU6050 configurations, first we have the **`MPU6050_ADDRESS_AD0_LOW `** (0X68), this is the default addres of the MPU6050 when the AD0 pin (addres pin) is tied to the ground (logic LOW). Then we have **`MPU6050_ADDRESS_AD0_HIGH `** (0x69), this the alternative address used when the AD0 pin is connected to VCC (logic HIGH). For third we have **`MPU6050_DEFAULT_ADRESS`** (0x68) This macro defines the default I2C address the program will use to communicate with the MPU6050. In this case, it is set to **`MPU6050_ADDRESS_AD0_LOW `**, meaning the AD0 pin is assumed to be connected to ground.

```ino
#include <Servo.h>
#include <Pixy2.h>
#include "Simple_MPU6050.h"
#include <Wire.h>

// MPU6050 Configuration
#define MPU6050_ADDRESS_AD0_LOW     0x68
#define MPU6050_ADDRESS_AD0_HIGH    0x69
#define MPU6050_DEFAULT_ADDRESS     MPU6050_ADDRESS_AD0_LOW
```

---

### 2. MPU6050, Pixy 2.1, an the Servo initialization:

This section of the code sets up essential components for the robot's operation: the MPU6050 sensor for orientation, the Pixy2 camera for vision processing, and a servo motor for steering.

The Simple_MPU6050 mpu; object is initialized to interface with the MPU6050 sensor, which measures the robot's rotation and acceleration. Two global variables, yawActual and yawInicial, are defined to track the current yaw (rotation around the vertical axis) and the initial yaw value, respectively. These variables are crucial for detecting and responding to changes in the robot's orientation during movement.

The Pixy2 pixy; object is created to control the Pixy2 camera, which can recognize visual patterns or objects. Although its specific use is not detailed in the current code, it is prepared for future tasks related to vision-based navigation or obstacle avoidance.

For steering, the Servo servoDireccion; object is declared. The servo is connected to pin 6, as defined by int pinServo = 6;. Predefined angles are assigned to constants (anguloIzquierda = 87, anguloCentro = 90, and anguloDerecha = 105) to represent left, center, and right steering positions, respectively. These angles ensure precise control of the servo for effective navigation. Additionally, int anguloMPU = 0; is introduced to dynamically adjust the steering angle based on real-time yaw readings from the MPU6050, enabling the robot to correct its path automatically.

This setup provides the foundation for integrating sensor data, visual feedback, and motor control to achieve smooth and responsive robotic movement.

```ino
Simple_MPU6050 mpu;
float yawActual = 0;  
float yawInicial = 0;

Pixy2 pixy;
Servo servoDireccion;
int pinServo = 6;
int anguloIzquierda = 87;
int anguloCentro = 90;
int anguloDerecha = 105;
int anguloMPU = 0;

```
---

### 3. Variables and Pin Configuration:

PD Controller Variables
Kp = 0.5, Kd = 0.5: PD gains for response and damping.
alpha = 0.15: Smooths steering adjustments.
lastError = 0: Previous error for derivative calculation.
curva = 0: Current turning action.
Robot State and Button
botonPin = A7: Button pin to start/stop movement.
enMarcha = false: Initial movement state (stopped).
anguloSuavizado = anguloCentro: Smoothed steering angle.
Vision Zones
Boundaries for camera detection:

deltaX, epsilonX, and zetaX ranges define vision zones.
Ultrasonic Sensor Pins
Left: trigIzquierdo = 10, echoIzquierdo = 9.
Center: trigCentro = 15, echoCentro = 14.
Right: trigDerecho = 7, echoDerecho = 8.
Motor Pins
motorPin1 = 5, motorPin2 = 4: Motor direction.
enablePin = 3, standbyPin = 16: Motor enable and standby.

```ino
float Kp = 0.5;
float Kd = 0.5;
float alpha = 0.15;
float lastError = 0;
int curva = 0;
const int botonPin = A7;  // button pin
bool enMarcha = false;    // initial state of the robot: stoped
float anguloSuavizado = anguloCentro;

const int deltaXMin = 88, deltaXMax = 98;
const int epsilonXMin = 101, epsilonXMax = 213;
const int zetaXMin = 190, zetaXMax = 274;

//Sensor pins
int trigIzquierdo = 10, echoIzquierdo = 9;
int trigCentro = 15, echoCentro = 14;
int trigDerecho = 7, echoDerecho = 8;

// Motor pins
int motorPin1 = 5, motorPin2 = 4, enablePin = 3, standbyPin = 16;

```

---

### 4. **`procesarMPU`** Function:
This function processes gyroscope and accelerometer data from the **`MPU6050`** sensor:

1- **`mpu.GetQuaternion`**, **`mpu.GetGravity`**, and **`mpu.GetYawPitchRoll`**: Extract quaternion, gravity vector, and yaw-pitch-roll angles.
2- **`mpu.ConvertToDegrees`**: Converts yaw-pitch-roll angles from radians to degrees.
3- Updates **`yawActual`**: The current yaw angle is stored globally for robot orientation.

This function ensures the robot can interpret and use orientation data for navigation and control.

**`inicializarControlPD Function
This function sets up the PD control by initializing the servo:

1- **`servoDireccion.attach(pinServo)`**: Links the servo to the specified pin for directional control.
2- Optionally centers the steering using a commented **`move_steer(anguloCentro)`** call, which positions the servo to a neutral angle.
It prepares the robot for smooth and precise directional adjustments.

**`move_steer`** Function
This function controls the servo motor for gradual steering adjustments:

1- Reads the current servo position using **`servoDireccion.read()`**.
2- If the target position is greater than the current position, the servo angle is incremented.
3- If the target position is smaller, the servo angle is decremented.
4- **`delay(10)`** ensures smooth transitions without abrupt movements.
This gradual movement prevents sudden turns, improving robot stability and precision during navigation.

```ino
// process data of the MP6050
void procesarMPU(int16_t *gyro, int16_t *accel, int32_t *quat, uint32_t *timestamp) {
    Quaternion q;
    VectorFloat gravity;
    float ypr[3] = { 0, 0, 0 };
    float xyz[3] = { 0, 0, 0 };
    
    mpu.GetQuaternion(&q, quat);
    mpu.GetGravity(&gravity, &q);
    mpu.GetYawPitchRoll(ypr, &q, &gravity);
    mpu.ConvertToDegrees(ypr, xyz);
    
    yawActual = (int)xyz[0];  // REFRESH YAW global variable
}
//*******
void inicializarControlPD() {
    servoDireccion.attach(pinServo);
    //move_steer(anguloCentro);
}
//*******
void move_steer(int pos) {
    int currentPos = servoDireccion.read();
    if (pos > currentPos) {
        for (int i = currentPos; i <= pos; i++) {
            servoDireccion.write(i);
            delay(10);
        }
    } else {
        for (int i = currentPos; i >= pos; i--) {
            servoDireccion.write(i);
            delay(10);
        }
    }
}
```

---

### 5.Functions for angle adjustment and distant measurement:

ajustarAngulo Function
This function adjusts the steering angle using PD control:

error and derivada calculate the proportional and derivative terms.
The angle is updated based on the error and constrained between anguloIzquierda and anguloDerecha.
move_steer(anguloDeseado) applies the adjusted angle.
It helps maintain smooth and precise steering.

medirDistancia Function
This function measures the distance using an ultrasonic sensor:

It triggers the sensor and calculates the distance based on the pulse duration.
It provides distance data for obstacle detection or navigation.

Angle Calculation Functions
calcularAnguloObjetivoI, calcularAnguloObjetivoDC, calcularAnguloObjetivoIC, and calcularAnguloObjetivoD Functions
These functions calculate the target steering angles for various curve types. The angle depends on the curva value:

Each curve type (based on curva % 4) has a unique angle to handle different turns.

```ino
void ajustarAngulo(float error, int anguloDeseado) {
    float derivada = error - lastError;
    float ajuste = (Kp * error) + (Kd * derivada);
    lastError = error;
    
    anguloDeseado += ajuste;
    anguloDeseado = constrain(anguloDeseado, anguloIzquierda, anguloDerecha);
    move_steer(anguloDeseado);
}
long medirDistancia(int trigPin, int echoPin) {
    digitalWrite(trigPin, LOW);
    delayMicroseconds(3);
    digitalWrite(trigPin, HIGH);
    delayMicroseconds(10);
    digitalWrite(trigPin, LOW);

    long duracion = pulseIn(echoPin, HIGH);
    return duracion * 0.034 / 2;
}

// Calculate specific angle I
int calcularAnguloObjetivoI(int curva) {
    if (curva % 4 == 1) return -75;     // Curvse 1, 5, 9, ...
    else if (curva % 4 == 2) return -165; // Curves 2, 6, 10, ...
    else if (curva % 4 == 3) return 105;   // Curves 3, 7, 11, ...
    else return 15;                      // Curves 4, 8, 12, ...
}

// calculate specific  DC
int calcularAnguloObjetivoDC(int curva) {
    if (curva % 4 == 1) return 90;     // Curves 1, 5, 9, ...
    else if (curva % 4 == 2) return 180; // Curves 2, 6, 10, ...
    else if (curva % 4 == 3) return -90;   // Curves 3, 7, 11, ...
    else return 0;                      // Curves 4, 8, 12, ...
}

// calculate specific angle IC
int calcularAnguloObjetivoIC(int curva) {
    if (curva % 4 == 1) return -90;     // Curves 1, 5, 9, ...
    else if (curva % 4 == 2) return -180; // Curves 2, 6, 10, ...
    else if (curva % 4 == 3) return 90;   // Curves 3, 7, 11, ...
    else return 0;                      // Curves 4, 8, 12, ...
}

//*******

// Calculate specific angle D
int calcularAnguloObjetivoD(int curva) {
    if (curva % 4 == 1) return 75;     // Curves 1, 5, 9, ...
    else if (curva % 4 == 2) return 165; // Curves 2, 6, 10, ...
    else if (curva % 4 == 3) return -105;   // Curves 3, 7, 11, ...
    else return -15;                      // Curves 4, 8, 12, ...
}
```

---

### 6. Motor Control Functions

avanzar Function
This function controls the forward movement of the robot:

1- motorPin1 is set to HIGH and motorPin2 to LOW, which activates the motor in the forward direction.
2- analogWrite(enablePin, velocidad) controls the motor speed by applying a PWM signal to the enable pin.
This function allows the robot to move forward at a specified speed.

retroceder Function
This function handles the backward movement of the robot:

1- motorPin1 is set to LOW and motorPin2 to HIGH to drive the motor in reverse.
2- analogWrite(enablePin, velocidad) adjusts the reverse speed of the motor using a PWM signal.
It enables the robot to move backward with the desired speed.

detener Function
This function stops the robot:

1- It sets both motorPin1 and motorPin2 to LOW, turning off the motor.
2- analogWrite(enablePin, 0) disables the motor by setting the PWM signal to 0.

```ino
//*******
void avanzar(int velocidad) {
    digitalWrite(motorPin1, HIGH);
    digitalWrite(motorPin2, LOW);
    analogWrite(enablePin, velocidad);
}
//*******
void retroceder(int velocidad) {
    digitalWrite(motorPin1, LOW);
    digitalWrite(motorPin2, HIGH);
    analogWrite(enablePin, velocidad);
}
//*******

void detener() {
    digitalWrite(motorPin1, LOW);
    digitalWrite(motorPin2, LOW);
    analogWrite(enablePin, 0);
}
```

---

### 7. DetectarCurva Function

The detectarCurva function manages the robot's behavior when encountering curves, based on sensor readings and gyroscopic data.

1- Distance and Error Calculations: It calculates error as the difference between distanciaIzquierda and distanciaDerecha, which helps determine the direction to steer. The sum of both distances helps validate curve conditions.

2- Pixy2 Object Detection: The Pixy2 camera checks for objects by calling pixy.ccc.getBlocks, and based on the detected signature (e.g., 4 or 5), it initiates curve detection logic.

3- Yaw-Angle Adjustment: It calculates AnguloObjetivo using predefined functions like calcularAnguloObjetivoIC or calcularAnguloObjetivoDC, depending on the context. Using the gyroscope, the robot adjusts its yaw angle by steering left or right with move_steer and moving with avanzar.

4- Lamp Feedback: The Pixy2 lamp provides visual feedback, turning on or off based on the robot's central distance.

5- Post-Curve Navigation: After navigating the curve, the robot advances while checking the central distance via medirDistancia, ensuring a clear path.

6- Curve Adjustment: Depending on the error, it adjusts the yaw angle further using calcularAnguloObjetivoD or calcularAnguloObjetivoI, steering left or right accordingly.

7- Straight Path Maintenance: If no curve is detected, the robot adjusts its angle to remain centered with ajustarAngulo, based on the calculated error, and continues advancing.

```ino
void detectarCurva(long distanciaIzquierda, long distanciaCentro, long distanciaDerecha) {
  
    float error = distanciaIzquierda - distanciaDerecha;
    lastError = error;
    float sum = distanciaIzquierda + distanciaDerecha;
    int AnguloObjetivo = 0;
    uint8_t signature ;
    unsigned long tiempoActual = millis();
    pixy.ccc.getBlocks();

    if (pixy.ccc.numBlocks > 0) {
        Serial.println(pixy.ccc.numBlocks);
        signature = pixy.ccc.blocks[0].m_signature;

        if (tiempoActual - tiempoUltimaCurva >= bloqueoTiempo) {
            if(signature == 4 || signature == 5){
                detener();
                delay(1000);
                if(bloqueadorI == true){
                    AnguloObjetivo = calcularAnguloObjetivoIC(curva);
                }
                else{
                    AnguloObjetivo = calcularAnguloObjetivoDC(curva);
                }
         
                // Verify conditions to start a turn
                if (yawActual <  AnguloObjetivo){
                    while (abs(yawActual - AnguloObjetivo) > 2) { // Tolerance of 2 degrees
                        mpu.dmp_read_fifo();  // Read gyroscope data
                        Serial.print("Yaw actual: ");
                        Serial.println(yawActual);
                        move_steer(75); // Turn to the left
                        avanzar(120); // Motor control during the turn
                    }
                }
                else if(yawActual > AnguloObjetivo){
                    //AnguloObjetivo = calcularAnguloObjetivo(curva);
                    while (abs(yawActual - AnguloObjetivo) > 2) { // Tolerance of 2 degrees
                        mpu.dmp_read_fifo();  // Read gyroscope data
                        Serial.print("Yaw actual: ");
                        Serial.println(yawActual);
                        move_steer(105); // Turn to the left
                        avanzar(120); // Motor control during the turn
                    }
                }
                detener();
                delay(1000);
                move_steer(90); // Turn to the left
                if(distanciaCentro > 30){ 
                    pixy.setLamp(0, 0);
                    delay(50);
                    pixy.setLamp(1, 0);
                }
                else pixy.setLamp(0, 0);
                delay(100);
      
                while(true){
                    long distanciaCentrowhile = medirDistancia(trigCentro, echoCentro);
                    Serial.print(" while Distancia Centro: "); Serial.println(distanciaCentrowhile);
                    avanzar(130);
                    delay(10);
                    if(distanciaCentrowhile <30) break;
                }

                detener();
                delay(1000);
                curva++ ;
                long distanciaIzquierda = medirDistancia(trigIzquierdo, echoIzquierdo);
                long distanciaDerecha = medirDistancia(trigCentro, echoCentro);
                if(error < -1 && sum > 100){
                    AnguloObjetivo = calcularAnguloObjetivoD(curva);
                    while (abs(yawActual - AnguloObjetivo) > 2) { // Tolerance of 2 degrees
                        mpu.dmp_read_fifo();  // Read gyroscope data
                        Serial.print("Yaw actual: ");
                        Serial.println(yawActual);
                        move_steer(119); // Turn to the left
                        retroceder(150); // Motor control during the turn
                    }
                }
                else if(error > 1 && sum > 100){
                    AnguloObjetivo = calcularAnguloObjetivoI(curva);
                    while (abs(yawActual - AnguloObjetivo) > 2) { // Tolerance of 2 degrees
                        mpu.dmp_read_fifo();  // Read gyroscope data
                        Serial.print("Yaw actual: ");
                        Serial.println(yawActual);
                        move_steer(69); // Turn to the left
                        retroceder(150); // Motor control during the turn
                    }
                }
                detener();
                delay(1000);
                move_steer(anguloCentro);
            }
        }
        tiempoUltimaCurva = tiempoActual;
    }
    else{
        ajustarAngulo(error, anguloCentro); // Maintain the center of the angle
        avanzar(120);
        // Print all the values
        Serial.print("Yaw: "); Serial.print(yawActual);
        Serial.print(" | Distancia Izquierda: "); Serial.print(distanciaIzquierda);
        Serial.print(" | Distancia Centro: "); Serial.print(distanciaCentro);
        Serial.print(" | Distancia Derecha: "); Serial.print(distanciaDerecha);
        Serial.print(" | Error: "); Serial.println(lastError);
    }
}

```

---

## References
- [Git Hub Readme Syntax](https://docs.github.com/en/get-started/writing-on-github/getting-started-with-writing-and-formatting-on-github/basic-writing-and-formatting-syntax)
- https://howtomechatronics.com/tutorials/arduino/ultrasonic-sensor-hc-sr04/
- https://www.sparkfun.com/products/15569
- https://invensense.tdk.com/products/motion-tracking/6-axis/mpu-6050/
- https://pixycam.com/2021/05/20/introducing-pixy-2-1/
- https://wro-association.org/wp-content/uploads/WRO-2023-Future-Engineers-Self-Driving-Cars-General-Rules.pdf
- https://www.onshape.com/en/
-https://www.matthewpeterkelly.com/tutorials/pdControl/index.html#:~:text=A%20proportional%2Dderivative%20(PD),car%20at%20some%20desired%20height.
- https://www.youtube.com/watch?v=TwFZ4BJUX5c&t=1805s
- https://grabcad.com/library/pixycam2-case-2

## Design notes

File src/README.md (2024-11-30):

Copy of TERRENATOR (30 x 18 cm) (5)

---

# Into the code

## Open Challenge
### **1. Libraries and Constants**

```cpp
#include <Servo.h>
#include "Simple_MPU6050.h"
#include <Wire.h>

#define MPU6050_ADDRESS_AD0_LOW     0x68
#define MPU6050_ADDRESS_AD0_HIGH    0x69
#define MPU6050_DEFAULT_ADDRESS     MPU6050_ADDRESS_AD0_LOW
```

**Explanation**:  
- Includes the necessary libraries for the project:  
  - `Servo.h`: For controlling the servo motor.  
  - `Simple_MPU6050.h`: A simplified library for working with the MPU6050 sensor, which measures orientation.  
  - `Wire.h`: Enables I2C communication, which the MPU6050 uses.  
- Defines the MPU6050’s I2C addresses. The default address `0x68` is used here.  

---

### **2. Global Variables**

```cpp
Simple_MPU6050 mpu;
float yawActual = 0;
float yawInicial = 0;

Servo servoDireccion;
int pinServo = 6;
int anguloIzquierda = 87;
int anguloCentro = 90;
int anguloDerecha = 105;
int anguloMPU = 0;

float Kp = 0.63;
float Kd = 0.4;
float alpha = 0.15;
float lastError = 0;
int curva = 0;
const int botonPin = A7;
bool enMarcha = false;
float anguloSuavizado = anguloCentro;

int trigIzquierdo = 9, echoIzquierdo = 10;
int trigCentro = 15, echoCentro = 14;
int trigDerecho = 7, echoDerecho = 8;

int motorPin1 = 5, motorPin2 = 4, enablePin = 3, standbyPin = 16;

unsigned long tiempoUltimaCurva = 0;
const long bloqueoTiempo = 2000;
int bloqueadorI = 65;
int bloqueadorD = 65;
```

**Explanation**:  
- **MPU6050 Variables**:  
  - `mpu`: Object to interact with the MPU6050 sensor.  
  - `yawActual` and `yawInicial`: Store the current and initial yaw (horizontal orientation).  
- **Servo Variables**:  
  - `servoDireccion`: Controls the robot’s steering.  
  - `anguloIzquierda`, `anguloCentro`, `anguloDerecha`: Represent the leftmost, center, and rightmost angles of the servo.  
- **PD Control**:  
  - `Kp` and `Kd`: Proportional and derivative gains for the control system.  
  - `lastError`: Stores the previous error to calculate the derivative.  
- **Robot State**:  
  - `curva`: Tracks the number of detected turns.  
  - `enMarcha`: Indicates whether the robot is moving.  
- **Ultrasonic Sensors**:  
  - Define pins for the left, center, and right sensors.  
- **Motor Pins**:  
  - Define the pins controlling motor speed and direction.  
- **Time Management**:  
  - `tiempoUltimaCurva`: Prevents the robot from detecting the same turn repeatedly.  
  - `bloqueadorI` and `bloqueadorD`: Set thresholds to determine when the robot can turn in a specific direction.  

---

### **3. MPU6050 Processing**

```cpp
void procesarMPU(int16_t *gyro, int16_t *accel, int32_t *quat, uint32_t *timestamp) {
    Quaternion q;
    VectorFloat gravity;
    float ypr[3] = { 0, 0, 0 };
    float xyz[3] = { 0, 0, 0 };
    
    mpu.GetQuaternion(&q, quat);
    mpu.GetGravity(&gravity, &q);
    mpu.GetYawPitchRoll(ypr, &q, &gravity);
    mpu.ConvertToDegrees(ypr, xyz);
    
    yawActual = (int)xyz[0];
}
```

**Explanation**:  
This function processes data from the MPU6050 to calculate the robot's yaw (horizontal rotation).  
- The quaternion, gravity vector, and yaw-pitch-roll angles are computed using the `Simple_MPU6050` library.  
- The result is stored in `yawActual` to be used in navigation.  

---

### **4. Servo Control**

```cpp
void inicializarControlPD() {
    servoDireccion.attach(pinServo);
}
```

**Explanation**:  
This function initializes the servo motor by attaching it to the specified pin (`pinServo`).

---

```cpp
void move_steer(int pos) {
    int currentPos = servoDireccion.read();
    if (pos > currentPos) {
        for (int i = currentPos; i <= pos; i++) {
            servoDireccion.write(i);
            delay(10);
        }
    } else {
        for (int i = currentPos; i >= pos; i--) {
            servoDireccion.write(i);
            delay(10);
        }
    }
}
```

**Explanation**:  
Moves the servo motor gradually to the desired position (`pos`) to ensure smooth transitions.

---

```cpp
void ajustarAngulo(float error, int anguloDeseado) {
    float derivada = error - lastError;
    float ajuste = (Kp * error) + (Kd * derivada);
    lastError = error;
    
    anguloDeseado += ajuste;
    anguloDeseado = constrain(anguloDeseado, anguloIzquierda, anguloDerecha);
    move_steer(anguloDeseado);
}
```

**Explanation**:  
- Uses a proportional-derivative (PD) controller to calculate adjustments to the servo angle based on the error.  
- The angle is constrained within the servo’s limits and applied smoothly using `move_steer`.  

---

### **5. Ultrasonic Sensors**

```cpp
long medirDistancia(int trigPin, int echoPin) {
    digitalWrite(trigPin, LOW);
    delayMicroseconds(3);
    digitalWrite(trigPin, HIGH);
    delayMicroseconds(10);
    digitalWrite(trigPin, LOW);

    long duracion = pulseIn(echoPin, HIGH);
    return duracion * 0.034 / 2;
}
```

**Explanation**:  
- Measures the distance using an ultrasonic sensor.  
- Sends a trigger pulse and measures the time for the echo to return, calculating the distance in centimeters.

---

### **6. Motor Control**

```cpp
void avanzar(int velocidad) {
    digitalWrite(motorPin1, HIGH);
    digitalWrite(motorPin2, LOW);
    analogWrite(enablePin, velocidad);
}
```

**Explanation**:  
Drives the motors forward at the specified speed (`velocidad`).

---

```cpp
void detener() {
    digitalWrite(motorPin1, LOW);
    digitalWrite(motorPin2, LOW);
    analogWrite(enablePin, 0);
}
```

**Explanation**:  
Stops the motors by turning off all outputs.

---

### **7. Curve Detection**

```cpp
void detectarCurva(long distanciaIzquierda, long distanciaCentro, long distanciaDerecha) {
    float error = distanciaIzquierda - distanciaDerecha;
    lastError = error;
    float sum = distanciaIzquierda + distanciaDerecha;

    unsigned long tiempoActual = millis();
    if (tiempoActual - tiempoUltimaCurva >= bloqueoTiempo) {
        if (error > 1 && distanciaCentro < 58 && sum > 90 && distanciaIzquierda > bloqueadorI) {
            // Left turn
        } else if (error < -1 && distanciaCentro < 58 && sum > 90 && distanciaDerecha > bloqueadorD) {
            // Right turn
        } else {
            ajustarAngulo(error, anguloCentro);
            avanzar(200);
        }
    } else {
        ajustarAngulo(error, anguloCentro);
        avanzar(200);
    }
}
```

**Explanation**:  
Detects curves based on differences in the distances measured by the ultrasonic sensors.  
- Determines whether to turn left or right based on the error.  
- Prevents repeated turn detection using a time-based lock (`bloqueoTiempo`).  

---

### **8. Setup Function**

```cpp
void setup() {
    Serial.begin(115200);
    // Pin configurations
    // Initialize servo and MPU6050
}
```

**Explanation**:  
- Sets up pin modes for input and output.  
- Initializes the servo and MPU6050 to start reading data.  
- Prepares the robot for operation.  

---

### **9. Loop Function**

```cpp
void loop() {
    if (!enMarcha) {
        // Waits until the button is pressed.
    }
    if (enMarcha) {
        // Reads MPU data and executes control logic.
    }
}
```

**Explanation**:  
- The robot remains idle until a button press sets it into motion.  
- Once active, the robot reads data from the MPU6050 and ultrasonic sensors, adjusts the servo, and controls the motors to navigate.

#Obstacle Challenge
```ino
#include <Servo.h> 
#include <Pixy2.h>
#include "Simple_MPU6050.h"
#include <Wire.h>

// MPU6050 configuration
#define MPU6050_ADDRESS_AD0_LOW 0x68
#define MPU6050_ADDRESS_AD0_HIGH 0x69
#define MPU6050_DEFAULT_ADDRESS MPU6050_ADDRESS_AD0_LOW

Simple_MPU6050 mpu;
float yawActual = 0;  // Global variable to store the current Yaw
// Variable for yaw
float yawInicial = 0;

// PD controller global variables
Pixy2 pixy;
Servo servoDireccion;
int pinServo = 6;
int anguloIzquierda = 75;
int anguloCentro = 90;
int anguloDerecha = 119;
int anguloMPU = 0;

float Kp = 0.5;
float Kd = 0.5;
float alpha = 0.15;
float lastError = 0;
int curva = 0;
const int botonPin = A7;  // Button pin
bool enMarcha = false;    // Initial state of the robot: stopped
float anguloSuavizado = anguloCentro;
int AnguloObjetivo = 0;

const int deltaXMin = 50, deltaXMax = 98;
const int epsilonXMin = 101, epsilonXMax = 213;
const int zetaXMin = 250, zetaXMax = 274;

// Sensor pins
int trigIzquierdo = 10, echoIzquierdo = 9;
int trigCentro = 15, echoCentro = 14;
int trigDerecho = 7, echoDerecho = 8;

// Motor pins
int motorPin1 = 5, motorPin2 = 4, enablePin = 3, standbyPin = 16;

// Time control
unsigned long tiempoUltimaCurva = 0;
const long bloqueoTiempo = 5000;
unsigned long tiempoUltimaCurvablo = 0;
const long bloqueoTiempoblo = 4000;
bool bloqueadorI = false;

// Function to process MPU6050 data
void procesarMPU(int16_t *gyro, int16_t *accel, int32_t *quat, uint32_t *timestamp) {
  Quaternion q;
  VectorFloat gravity;
  float ypr[3] = { 0, 0, 0 };
  float xyz[3] = { 0, 0, 0 };

  mpu.GetQuaternion(&q, quat);
  mpu.GetGravity(&gravity, &q);
  mpu.GetYawPitchRoll(ypr, &q, &gravity);
  mpu.ConvertToDegrees(ypr, xyz);

  yawActual = (int)xyz[0];  // Update global Yaw
}

// Function to initialize the PD controller
void inicializarControlPD() {
  servoDireccion.attach(pinServo);
}

// Function to smoothly move the servo to a position
void move_steer(int pos) {
  int currentPos = servoDireccion.read();
  if (pos > currentPos) {
    for (int i = currentPos; i <= pos; i++) {
      servoDireccion.write(i);
      delay(10);
    }
  } else {
    for (int i = currentPos; i >= pos; i--) {
      servoDireccion.write(i);
      delay(10);
    }
  }
}

// Function to adjust the steering angle based on error
void ajustarAngulo(float error, int anguloDeseado) {
  float derivada = error - lastError;
  float ajuste = (Kp * error) + (Kd * derivada);
  lastError = error;

  anguloDeseado += ajuste;
  anguloDeseado = constrain(anguloDeseado, anguloIzquierda, anguloDerecha);
  move_steer(anguloDeseado);
}

// Function to measure distance using an ultrasonic sensor
long medirDistancia(int trigPin, int echoPin) {
  digitalWrite(trigPin, LOW);
  delayMicroseconds(3);
  digitalWrite(trigPin, HIGH);
  delayMicroseconds(10);
  digitalWrite(trigPin, LOW);

  long duracion = pulseIn(echoPin, HIGH);
  return duracion * 0.034 / 2;
}

// Function to calculate the target angle for left curves
int calcularAnguloObjetivoI(int curva) {
  if (curva % 4 == 1) return -75;        // Curves 1, 5, 9, ...
  else if (curva % 4 == 2) return -165;  // Curves 2, 6, 10, ...
  else if (curva % 4 == 3) return 105;   // Curves 3, 7, 11, ...
  else return 15;                        // Curves 4, 8, 12, ...
}

// Function to calculate the target angle for right curves
int calcularAnguloObjetivoD(int curva) {
  if (curva % 4 == 1) return 70;         // Curves 1, 5, 9, ...
  else if (curva % 4 == 2) return 165;   // Curves 2, 6, 10, ...
  else if (curva % 4 == 3) return -110;  // Curves 3, 7, 11, ...
  else return -15;                       // Curves 4, 8, 12, ...
}

// Function to move the robot forward
void avanzar(int velocidad) {
  digitalWrite(motorPin1, HIGH);
  digitalWrite(motorPin2, LOW);
  analogWrite(enablePin, velocidad);
}

// Function to move the robot backward
void retroceder(int velocidad) {
  digitalWrite(motorPin1, LOW);
  digitalWrite(motorPin2, HIGH);
  analogWrite(enablePin, velocidad);
}

// Function to stop the robot
void detener() {
  digitalWrite(motorPin1, LOW);
  digitalWrite(motorPin2, LOW);
  analogWrite(enablePin, 0);
}
//*******
void detectarCurva(long distanciaIzquierda, long distanciaCentro, long distanciaDerecha) {
  float error = distanciaIzquierda - distanciaDerecha;
  lastError = error;
  float sum = distanciaIzquierda + distanciaDerecha;

  if (distanciaIzquierda < 35 && sum < 100) {
    move_steer(110);
    avanzar(100);
    delay(10);
  } else if (distanciaDerecha < 35 && sum < 100) {
    move_steer(85);
    avanzar(100);
    delay(10);
  } else if (error < -1 && sum > 100 && distanciaCentro < 50) {
    while (true) {
      mpu.dmp_read_fifo();
      pixy.ccc.getBlocks();
      avanzar(100);
      move_steer(69);
      if (signature == 1 || signature == 2 || abs(yawActual - AnguloObjetivo) > 5) break;
    }
    detener();
    delay(100);
  } else if (error > 1 && sum > 100 && distanciaCentro < 50) {
    while (true) {
      mpu.dmp_read_fifo();
      pixy.ccc.getBlocks();
      avanzar(100);
      move_steer(119);
      if (signature == 1 || signature == 2 || abs(yawActual - anguloObjetivo) > 2) break;
    }
    detener();
    delay(100);
  } else {
    move_steer(90);
    avanzar(100);
  }
}

void detectarBloques() {
  long distanciaIzquierda = medirDistancia(trigIzquierdo, echoIzquierdo);
  long distanciaCentro = medirDistancia(trigCentro, echoCentro);
  long distanciaDerecha = medirDistancia(trigDerecho, echoDerecho);
  unsigned long tiempoActualblo = millis();
  float sum = distanciaIzquierda + distanciaDerecha;
  if (tiempoActualblo - tiempoUltimaCurvablo >= bloqueoTiempoblo) {
    pixy.ccc.getBlocks();
    avanzar(100);
    if (pixy.ccc.numBlocks > 0) {
      Serial.println(pixy.ccc.numBlocks);

      for (int i = 0; i < pixy.ccc.numBlocks; i++) {
        uint8_t signature = pixy.ccc.blocks[i].m_signature;
        int x = pixy.ccc.blocks[i].m_x;

        // Comprobación de la firma y región para signature 1
        if (signature == 1) {
          while (x < zetaXMin) {
            avanzar(100);
            move_steer(119);  // Turn left
            pixy.ccc.getBlocks();
            if (pixy.ccc.numBlocks > 0) {
              for (int i = 0; i < pixy.ccc.numBlocks; i++) {
                x = pixy.ccc.blocks[i].m_x;
                Serial.println("verde detectado");
                delay(10);
              }
            }
          }
          move_steer(73);
          delay(180);
          move_steer(90);
          delay(500);
          long distanciaIzquierda = medirDistancia(trigIzquierdo, echoIzquierdo);
          long distanciaCentro = medirDistancia(trigCentro, echoCentro);
          long distanciaDerecha = medirDistancia(trigDerecho, echoDerecho);
          float error = distanciaIzquierda - distanciaDerecha;
          lastError = error;
          float sum = distanciaIzquierda + distanciaDerecha;
          if (sum< 110 / error > 10) {
            move_steer(119);
            delay(300);
            move_steer(70);
            delay(100);
            move_steer(90);
          } else if (sum < 110 && error < -10) {
            move_steer(69);
            delay(300);
            move_steer(119);
            delay(50);
            move_steer(90);
          } else {
            move_steer(90);
          }
          tiempoUltimaCurvablo = tiempoActualblo;
        }
        // Comprobación de la firma y región para signature 2
        else if (signature == 2) {
          while (x > deltaXMin) {
            avanzar(100);
            move_steer(69);  // Turn right
            pixy.ccc.getBlocks();
            if (pixy.ccc.numBlocks > 0) {
              for (int i = 0; i < pixy.ccc.numBlocks; i++) {
                x = pixy.ccc.blocks[i].m_x;
                Serial.println("rojo detectado");
              }
            }
          }
          move_steer(119);
          delay(180);
          move_steer(90);
          delay(500);
          long distanciaIzquierda = medirDistancia(trigIzquierdo, echoIzquierdo);
          long distanciaCentro = medirDistancia(trigCentro, echoCentro);
          long distanciaDerecha = medirDistancia(trigDerecho, echoDerecho);
          float error = distanciaIzquierda - distanciaDerecha;
          lastError = error;
          if (sum < 110 && error > 10) {
            move_steer(119);
            delay(300);
            move_steer(70);
            delay(100);
            move_steer(90);
          } else if (sum < 110 && error < -10) {
            move_steer(69);
            delay(300);
            move_steer(119);
            delay(50);
            move_steer(90);
          } else {
            move_steer(90);
          }
        }
        tiempoUltimaCurvablo = tiempoActualblo;
      }
    }
  }

  else {
    detectarCurva(distanciaIzquierda, distanciaCentro, distanciaDerecha);
  }
}
//*******
void actualizar() {
  long distanciaIzquierda = medirDistancia(trigIzquierdo, echoIzquierdo);
  long distanciaCentro = medirDistancia(trigCentro, echoCentro);
  long distanciaDerecha = medirDistancia(trigDerecho, echoDerecho);

  detectarBloques();
  //detectarCurva(distanciaIzquierda, distanciaCentro, distanciaDerecha);

  if (curva == 12) {
    move_steer(90);
    delay(700);
    detener();
    delay(60000);
  }
  /*   // Imprimir todos los valores
    Serial.print("Yaw: "); Serial.print(yawActual);
    Serial.print(" | Distancia Izquierda: "); Serial.print(distanciaIzquierda);
    Serial.print(" | Distancia Centro: "); Serial.print(distanciaCentro);
    Serial.print(" | Distancia Derecha: "); Serial.print(distanciaDerecha);
    Serial.print(" | Error: "); Serial.println(lastError);*/
}
void setup() {
  Serial.begin(115200);
  Wire.begin();
  Wire.setClock(400000);
  if (pixy.init() == 0) {
    Serial.println("Pixy2 inicializado correctamente");
  } else {
    Serial.println("Error al inicializar Pixy2");
    while (true)
      ;  // Detener el programa si falla la inicialización
  }

  // Iniciate pins
  pinMode(trigIzquierdo, OUTPUT);
  pinMode(echoIzquierdo, INPUT);
  pinMode(trigCentro, OUTPUT);
  pinMode(echoCentro, INPUT);
  pinMode(trigDerecho, OUTPUT);
  pinMode(echoDerecho, INPUT);

  pinMode(motorPin1, OUTPUT);
  pinMode(motorPin2, OUTPUT);
  pinMode(enablePin, OUTPUT);
  pinMode(standbyPin, OUTPUT);
  digitalWrite(standbyPin, HIGH);

  // Iniciate PD
  inicializarControlPD();

  // Iniciate MPU6050
  Serial.println(F("Iniciando calibración del MPU6050..."));
  mpu.SetAddress(MPU6050_ADDRESS_AD0_LOW)
    .CalibrateMPU()
    .load_DMP_Image();
  mpu.on_FIFO(procesarMPU);
  pixy.setLamp(1, 0);

  delay(100);
}
void loop() {
  if (!enMarcha) {  // If the robot is NOT going
    delay(100);
    if (analogRead(botonPin) == 0) {  // If the botton is press
      enMarcha = true;                // Change state to "en marcha"
      Serial.println("¡Robot en marcha!");
      move_steer(anguloCentro);
    } else {
      detener();  // keep the robot stopped
    }
  }
  if (enMarcha == true) {  // If the robot is going
    //pixy.setLamp(0, 0);
    mpu.dmp_read_fifo();  // Read MPU6050 lectures
    actualizar();         // Do PD control
    delay(5);
  }
}
```

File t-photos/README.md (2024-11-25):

# Team Photos

---

## Turkiye Official Photo


## Funny Photo


---

## Old Oficial photo
foto oficial

## Old Funny photo
foto funny

---

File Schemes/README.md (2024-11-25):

# Circuit diagram

Copy of TERRENATOR (30 x 18 cm) (2)

here you can find the circuit that integrates our robot that will go to turkey, as well as we can find a small explanation of it.
<br>
 <br>

 > [!NOTE]
>The schemes of the circuit was made in [Fritzing](https://fritzing.org/)

<br>

---

Circuit Diagram

---

### Explanation:

---

1- Microcontroller (Arduino Nano):
The central component managing all sensors and actuators. It receives signals, 
processes them, and sends output to the connected devices.

---

2- HC-SR04 Ultrasonic Sensors:
The top section of the diagram shows multiple HC-SR04 sensors (typically used for distance measurement). Each sensor has four pins:

VCC: Power supply, connected to the 5V pin of the Arduino.
GND: Ground, connected to Arduino's GND.
TRIG: Trigger pin, connected to individual Arduino digital pins.
ECHO: Echo pin, also connected to digital pins.
These sensors measure distance by sending ultrasonic waves and timing their return.

---

3- MPU6050 (Gyroscope + Accelerometer):
On the left, an MPU6050 module is visible.

VCC and GND are connected to the Arduino's power pins.
SCL and SDA are connected to the Arduino's I2C pins (A5 and A4, respectively, on the Nano).
This module provides orientation and motion data.

---

4- Servo Motor:
Below the MPU6050, a servo motor is connected.

Signal Pin: Goes to an Arduino PWM pin (likely pin 9).
Power and Ground: Connected to an external power supply for adequate current.

---

5- L298N Motor Driver:
Near the motor, there is an L298N or TB6612 motor driver module controlling the DC motor.

Power Input (12V): Supplied from the battery (bottom right).
Output Pins: Connected to the motor terminals for forward/backward movement.
Control Pins: Connected to Arduino digital pins for controlling speed and direction.

---

6- DC Motor:
Connected to the motor driver outputs. This motor is powered by the 12V supply and controlled by the Arduino via the driver.

---

7- Power Supply (Battery Pack):
A 12V Li-ion battery supplies power to the motor driver and, indirectly, to the Arduino.

A voltage regulator is likely used to step down 12V to 5V for the Arduino and other components.

---

8- Switch:
A power switch between the battery and the circuit ensures safe operation and easy ON/OFF control.

---

9- Resistors and Capacitors:
Passive components are included for stability and noise reduction, particularly around the MPU6050 and SD card module.

---

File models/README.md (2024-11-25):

# Models
Copy of TERRENATOR (30 x 18 cm) (3)

Here are you can find all the 3D print Parts of the robot.

<br>
 <br>

 > [!NOTE]
> If you want to see all the complete robot with an voiceover video tutorial click [here](https://www.youtube.com/@TERRENATORTEAM)

<br>

## Models and 3D parts explanations

<br>
 <br>

 > [!NOTE]
> All this can be find in the main [README](https://github.com/kieviceb/TERRENATOR-WRO-2024/blob/main/README.md)

<br>

In the chassis and 3D part, you can find all the 3D parts that made up the robot that won in Panama in the old models part.

So the chassis and the design of the car that will go to Turkey took a long time because our ideas were to make the robot of the national competition much smaller, agile, faster and prettier, so we had to make a completely new chassis, in this one changing several parts of the assembly, for example in the steering system, since in our previous robot, the steering system was based on moving a cylinder with teeth that moved a line with teeth that gave direction to the robot, the problem with this steering design was that it is a bit imprecise so, we adopted a steering design similar to the Ackerman steering, and we also changed the servo motor.

---
<p align="center">
  Imagen 1
  Imagen 2
</p>
---

Then for the traction, we have four parts, the big gear for motor that this is the gear that give us the torque to move the robot, we have a game of gears that we can modify in case we need speed or more torque, and we have a fixed drive motor retainer, here we have a support for the motor, and we have the small gear for the drive axle, and we have the traction support.

---
<p align="center">
  Imagen 1
  Imagen 2
</p>

---
Then we have the skeleton: 
Here in the skeleton is the main base chasis of the robot, here we can find in the physical one the motor game with his gears, the servo motor, and the modifications that make the steering have better movements.

And also here we have the main shell, here we can find all that makes our robot, here are all the circuits for the robot and the base for the camera.

---
<p align="center">
  Imagen 1
  Imagen 2
</p>

---

Now for the sensors, we have made a lot of support for them, but with this one we made the correct one, it is more outside beacuase they give us better data in this way.

---

<p align="center">
  Imagen 1
</p>

---

Now with the wheels, we have designed it by ourself, because in that way we can ajust eveything by ourself and it's so much better in that way. For the traction wheels they are a little bit so more big.

---
<p align="center">
  Imagen 1
  Imagen 1
</p>

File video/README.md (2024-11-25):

# VIDEO

---

Copy of TERRENATOR (30 x 18 cm) (1)

Click down below for the demonstration of the first round of our robot.

[CLICK HERE!](https://www.youtube.com/@TERRENATORTEAM)

---

Copy of TERRENATOR (30 x 18 cm)

Click dowon here to go to the video of the second challenge of the WRO Future Engineers category.

[CLICK HERE!](https://www.youtube.com/@TERRENATORTEAM)

---

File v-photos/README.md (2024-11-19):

# Vehicle Photos

## International Final car

| Front | Right | Back |
|:---:|:---:|:---:|
| front |front |  front |
| Left | Top | Bottom |
|front| front | front|

## National Final car previous prototype

| Front | Right | Back |
|:---:|:---:|:---:|
|front_old-removebg-preview|National_final_right_side-removebg-preview|National_Final_Back_side-removebg-preview|
| Left | Top | Bottom |
| left_old-removebg-preview |National_Final_upper_side-removebg-preview|National_Final_Down_side-removebg-preview|

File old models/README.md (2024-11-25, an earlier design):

# Old Model Robot and his 3D parts

Copy of TERRENATOR (30 x 18 cm) (4)

Here you will find all the assmbly and 3D parts of the robot that win in Panama, that make us go to Turkiye.

<br>
 <br>

 > [!NOTE]
>All the assembly of the robot and the design of all the parts were made in [OnShape](https://www.onshape.com/en/), and printed with UltiMaker [CURA](https://ultimaker.com/es/software/ultimaker-cura/)

<br>

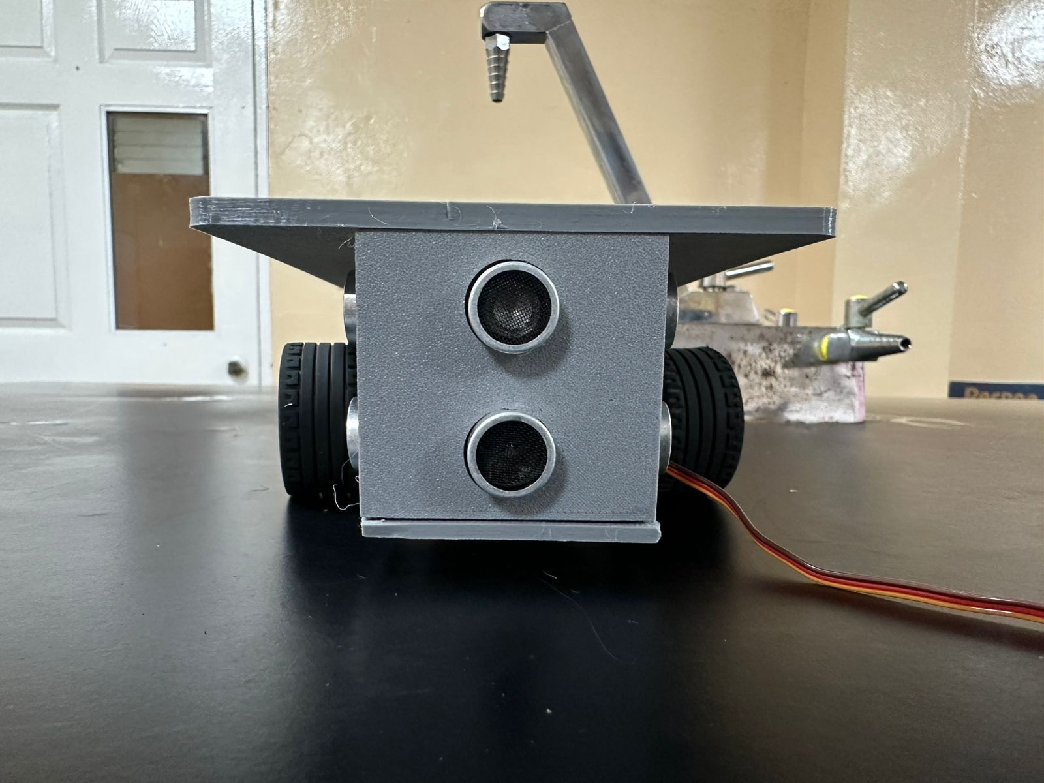
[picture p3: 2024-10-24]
v-photos/b7dfa661-fe1c-4ad1-a0f2-22e0b82da022.jpg

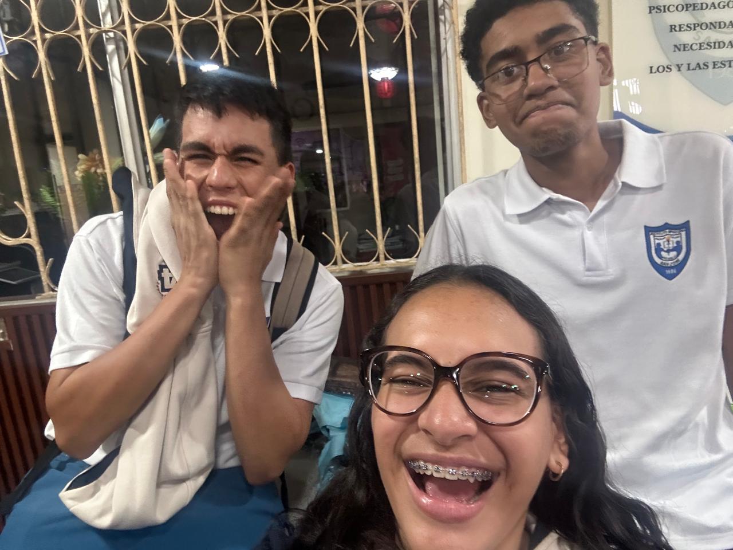
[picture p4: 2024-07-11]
t-photos/foto funny.jpeg

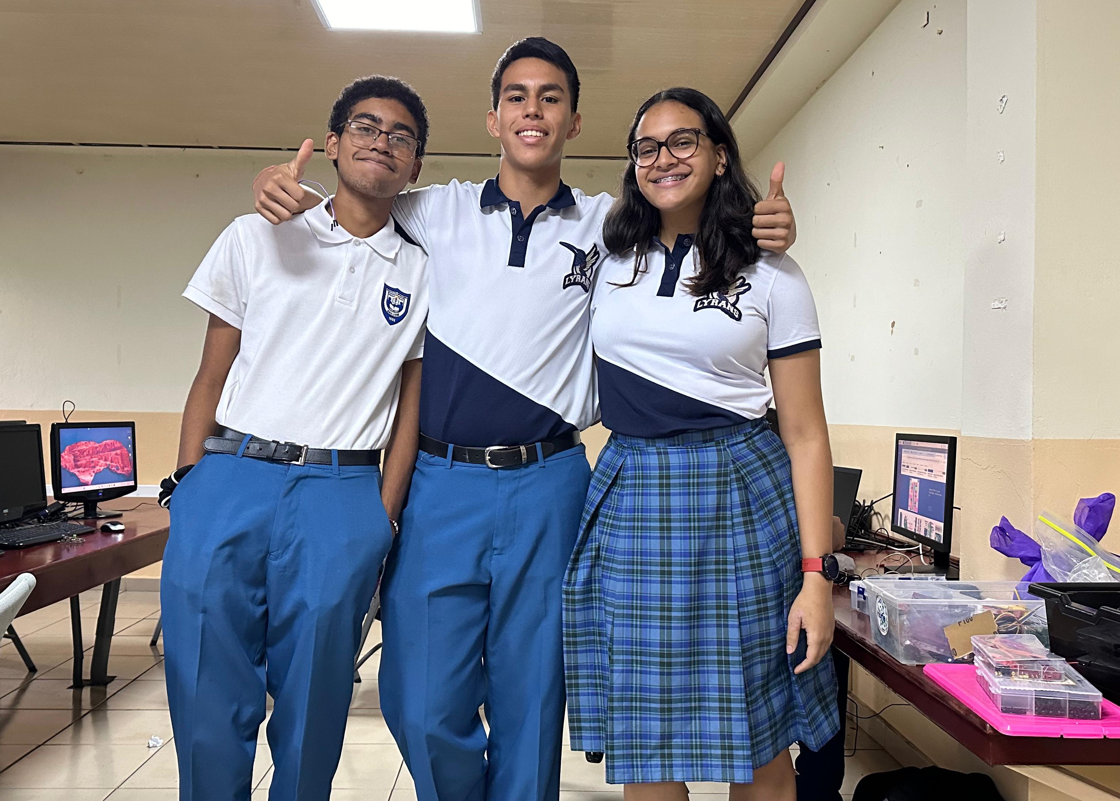
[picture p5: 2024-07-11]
t-photos/foto oficial.jpeg

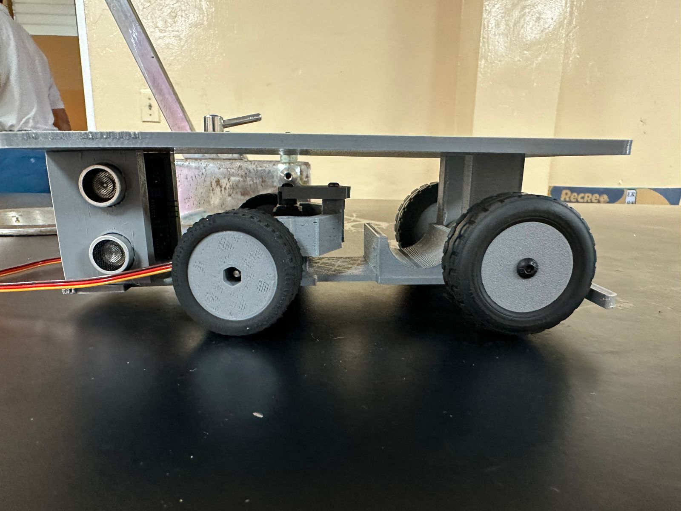
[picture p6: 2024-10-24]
v-photos/Internaional First Prototype.jpg

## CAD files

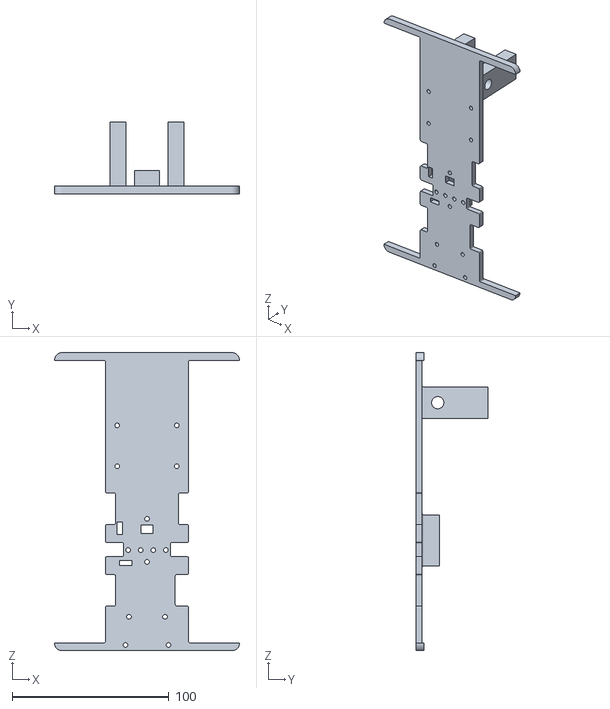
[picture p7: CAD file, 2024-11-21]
models/skeleton/main skeleton.stl
118.0 x 46.0 x 190.0

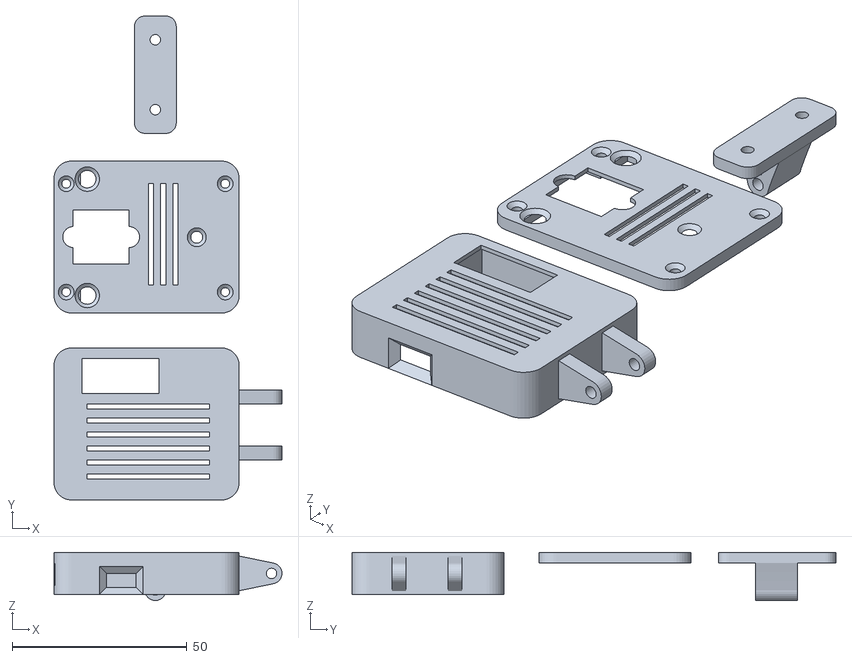
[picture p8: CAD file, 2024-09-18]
models/PixyCam v2 case.stl
65.2 x 138.5 x 13.8

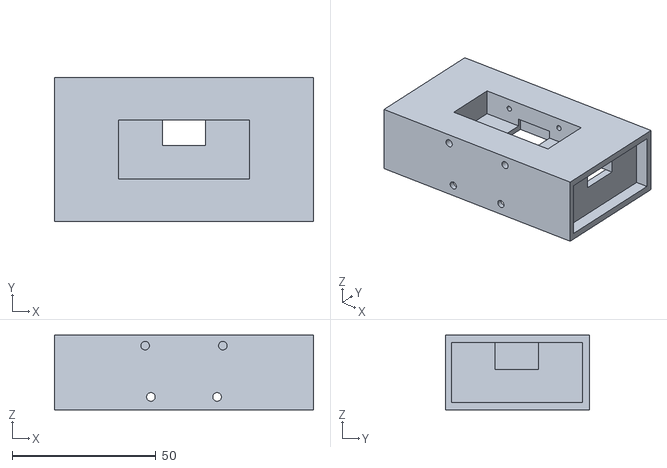
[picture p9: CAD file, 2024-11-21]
models/sensors/Ultrasonic sensors support.stl
90.0 x 50.0 x 26.0

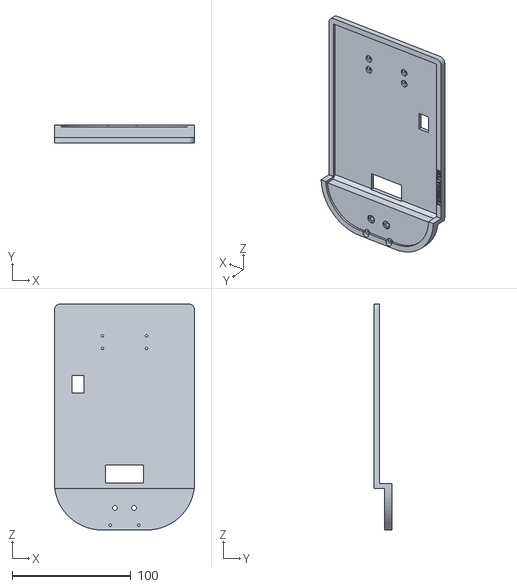
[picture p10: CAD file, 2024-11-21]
models/skeleton/shell.stl
118.0 x 15.5 x 190.0

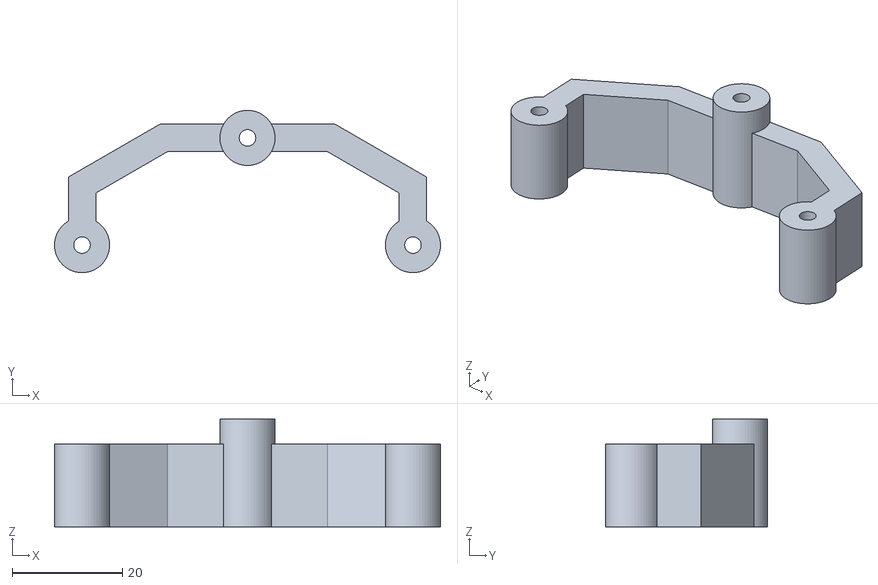
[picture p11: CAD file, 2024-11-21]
models/steering and traction/steering/principal steering turning guide.stl
70.0 x 29.4 x 19.5

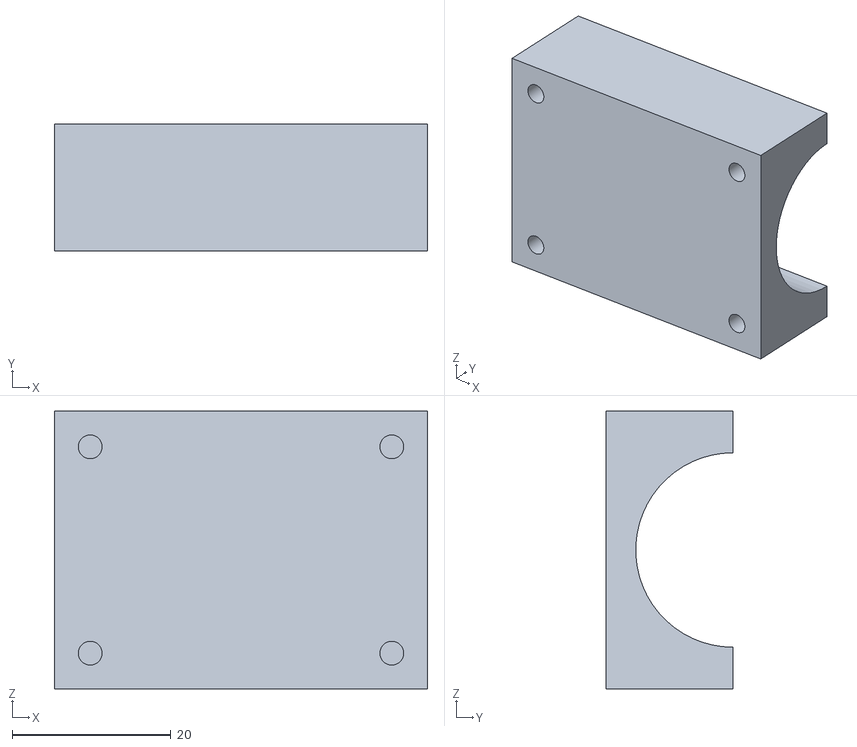
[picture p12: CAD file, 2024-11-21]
models/steering and traction/traction/traction support for fixed engine.stl
47.0 x 16.0 x 35.0

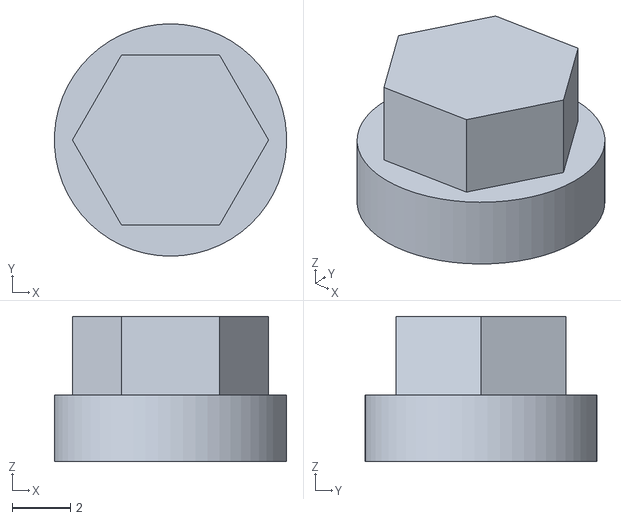
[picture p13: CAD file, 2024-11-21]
models/wheels/steering rim rhinestone cup.stl
7.99 x 8.00 x 5.00

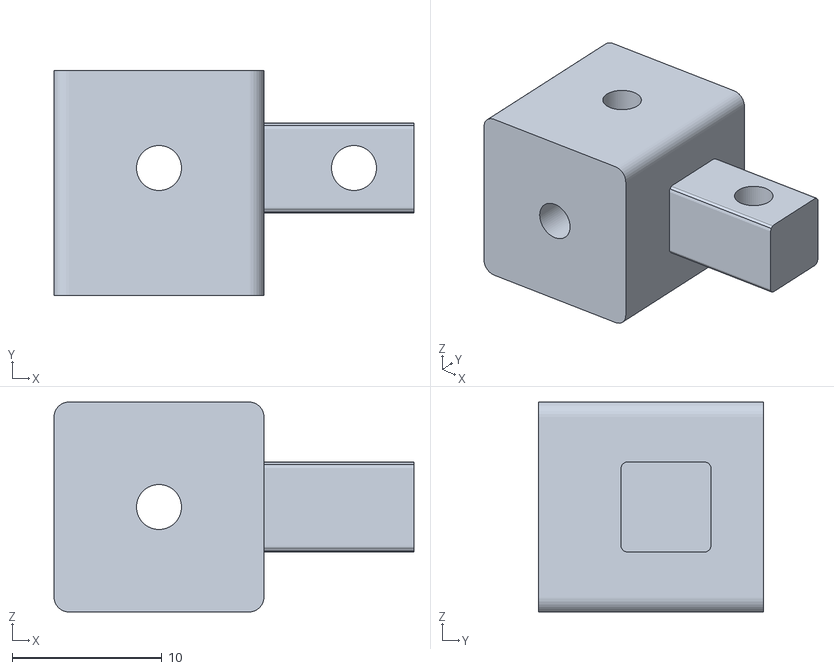
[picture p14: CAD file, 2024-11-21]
models/steering and traction/steering/rotative wheels axle support.stl
24.0 x 15.0 x 14.0

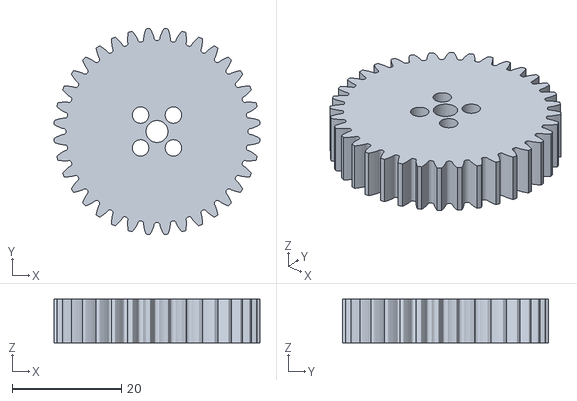
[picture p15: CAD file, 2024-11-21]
models/steering and traction/traction/big gear for motor.stl
37.7 x 37.7 x 8.00

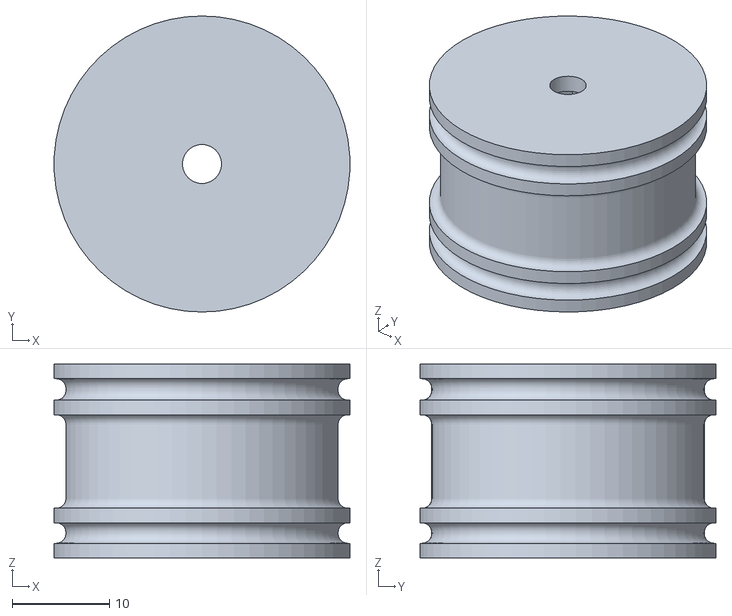
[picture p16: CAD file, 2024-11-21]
models/wheels/steering tire rim.stl
30.4 x 30.4 x 19.9

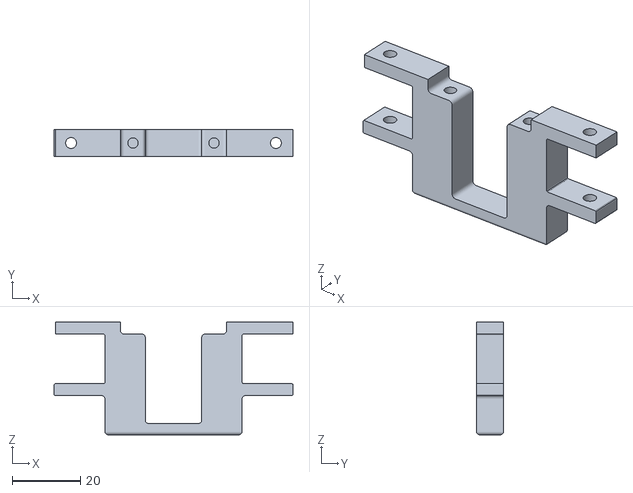
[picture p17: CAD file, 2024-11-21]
models/steering and traction/steering/steering axle support.stl
70.0 x 8.00 x 33.0

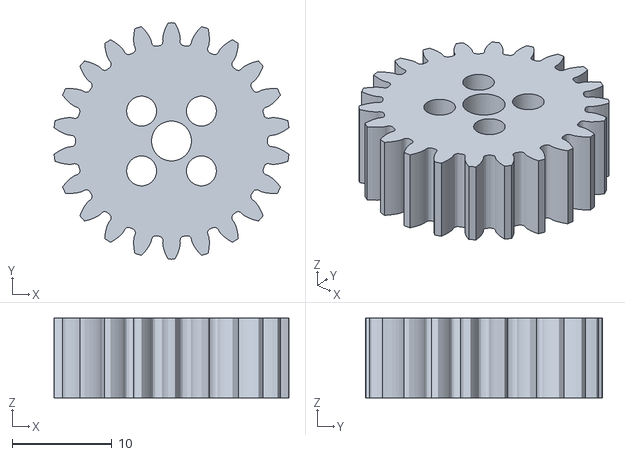
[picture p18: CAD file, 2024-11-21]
models/steering and traction/traction/small gear for the drive axle.stl
23.6 x 23.7 x 8.00

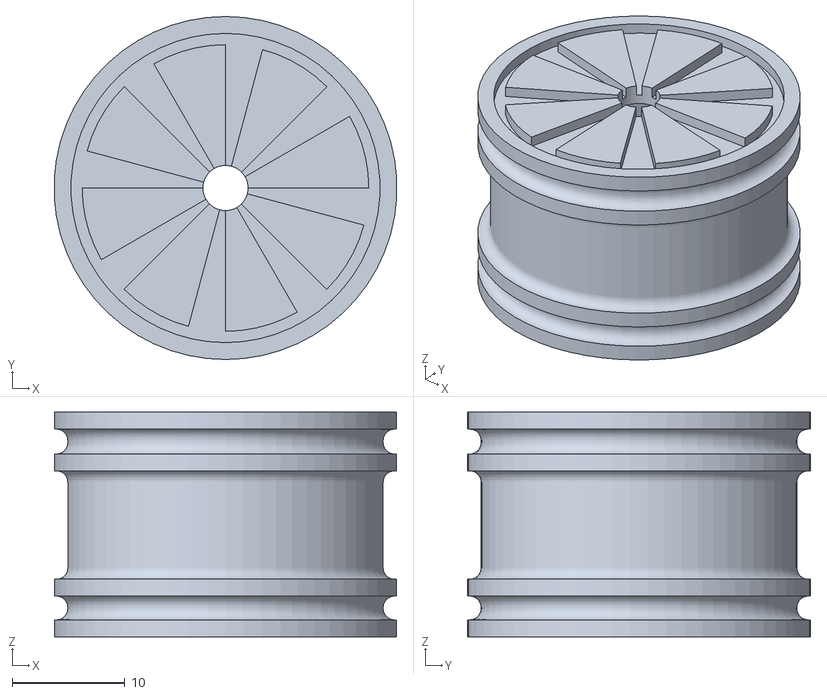
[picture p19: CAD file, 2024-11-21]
models/wheels/traction tire rim.stl
30.4 x 30.4 x 19.9

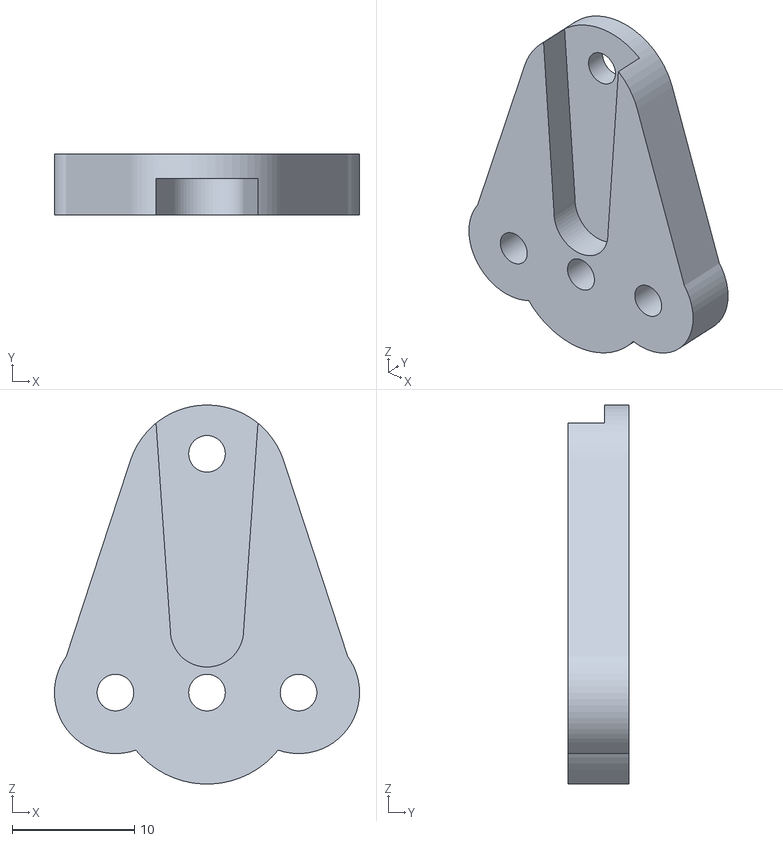
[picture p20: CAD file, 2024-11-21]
models/steering and traction/steering/servo motor to steering guide.stl
25.0 x 5.00 x 31.1

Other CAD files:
models/steering and traction/traction/fixed drive motor retainer.stl
old models/FULL ASSEMBLY.stl
old models/ASSEMBLY.stl
old models/MOTOR SMALL ENGINE.stl
old models/DIRECTION BAR TEETH.stl
old models/DIRECTION PART 1.stl
old models/DIRECTION SUPPORT.stl
old models/FRONT ULTRASONIC SENSOR SUPPORT.stl
old models/LOWER BASE.stl
old models/MOTOR BAR CONNECTORS.stl
old models/MOTOR BIG ENGINE.stl
old models/MOTOR ENGINE BAR.stl
old models/MOTOR SUPPORT PART 1.stl
old models/MOTOR SUPPORT PART 2.stl
old models/SERVO BOX.stl
old models/TRACTION GEAR.stl
old models/TRACTION SMALL BAR.stl
old models/UPPER BASE (1).stl
old models/WHEEL ELBOWS.stl

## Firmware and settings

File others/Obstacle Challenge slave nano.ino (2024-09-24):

#include <ESP32Servo.h>
#include <Wire.h>
#include <Arduino.h>

#define SLAVE_ADDR 9  // Slave device address

// Ultrasonic sensor pins
const int trigLeft = 11;
const int echoLeft = 12;
const int trigCenter = 9;
const int echoCenter = 10;
const int trigRight = 7;
const int echoRight = 8;
const int led = 13;  // Pin for an indicator LED

// Motor TB6612 pins
const int motorPin1 = 4;
const int motorPin2 = 5;
const int enablePin = 2; // PWM for speed control
const int standbyPin = 3; // STBY to enable the motor

// Servo and direction
Servo servo;  // Create a Servo object
const int pinServo = 6; // Servo pin
const int angleLeft = 60;  // Servo angle for left
const int angleCenter = 95; // Center angle (straight ahead)
const int angleRight = 130; // Servo angle for right
char region;  // Variable to store detected region
int signature;  // Variable to store block signature
volatile bool dataReceived = false;  // Flag to indicate if data is received
int lane = 0;  // Variable to determine the lane
int turnCount = 0;  // Counter for the number of turns made
unsigned long lastActionTime = 0;  // Variable to store the time of the last action
const long lockoutTime = 2000;  // 2 seconds lockout time between actions

// Distance variables for ultrasonic sensors
long distanceLeft;
long distanceCenter;
long distanceRight;

// Function to measure distance using the ultrasonic sensors
long measureDistance(int trigPin, int echoPin) {
  digitalWrite(trigPin, LOW);
  delayMicroseconds(2);
  digitalWrite(trigPin, HIGH);
  delayMicroseconds(10);
  digitalWrite(trigPin, LOW);

  long duration = pulseIn(echoPin, HIGH);  // Measure the round-trip time of the pulse
  long distance = duration * 0.034 / 2;   // Convert the time into distance (cm)

  return distance;  // Return the measured distance
}

// Function to move the robot forward at a specific speed
void moveForward(int speed) {
  digitalWrite(motorPin1, HIGH);  // Activate the motor in forward direction
  digitalWrite(motorPin2, LOW);   // Motor forward direction
  analogWrite(enablePin, speed);  // Apply PWM for speed control
}

// Function to stop the motor
void stopMotor() {
  digitalWrite(motorPin1, LOW);  // Turn off motor
  digitalWrite(motorPin2, LOW);  // Turn off motor
  analogWrite(enablePin, 0);     // Stop the motor
}

// Functions for different actions based on the region and detected signature
void greendelta() {
  Serial.println("Executing left bypass maneuver...");
  moveForward(200);  // Move forward at speed 200
  servo.write(50);  // Turn the servo left (angle 50)
  delay(1000);      // Wait for 1 second
  servo.write(130); // Turn the servo right (angle 130)
  delay(500);       // Wait for 500 ms
  servo.write(angleCenter);  // Return the servo to the center

  moveForward(200);  // Continue moving forward
  delay(10);         // Small delay to avoid erratic readings
  servo.write(130);  // Turn right again
  delay(1000);       // Wait for 1 second
  servo.write(50);   // Turn left again
  delay(500);        // Wait for 500 ms
  servo.write(angleCenter);  // Return to the center
  Serial.println("Action: Green delta.");
}

// Similar functions for other regions, adjusting the servo movement and behavior
void greenepsilon() {
  servo.write(60);  // Move the servo to 60 degrees
  delay(2000);      // Wait for 2 seconds
  servo.write(95);  // Return to center
  Serial.println("Action: Green epsilon");
}

void greenzeta() {
  servo.write(60);  // Move the servo to 60 degrees
  delay(2000);      // Wait for 2 seconds
  servo.write(95);  // Return to center
  Serial.println("Action: Green zeta");
}

// Function to execute an action based on the region and detected signature
void executeAction (char region, int signature) {
  Serial.print("Executing action for Signature ");
  Serial.print(signature);
  Serial.print(" in Region ");
  Serial.println(region);
  
  if (signature == 2) {  // If the detected signature is 2 (green)
    switch (region) {
      case 'D': greendelta(); break;
      case 'E': greenepsilon(); break;
      case 'Z': greenzeta(); break;
      // More cases can be added if desired
    }
  } else if (signature == 4) {  // If the detected signature is 4 (red)
    // Similar code can be added to handle red signatures
  }
}

// Function that executes when data is received via I2C
void receiveData(int byteCount) {
  if (byteCount >= 2) {  // Expecting 2 bytes: region and signature
    region = Wire.read();      // Read the region
    signature = Wire.read();   // Read the signature

    Serial.print("Data received - Region: ");
    Serial.print(region);
    Serial.print(", Signature: ");
    Serial.println(signature);
    dataReceived = true;

    moveForward(200);  // Move forward at a moderate speed
  }
}

void setup() {
  Serial.begin(115200);  // Start serial communication
  delay(500);  // Small delay to ensure communication is ready

  // Setup pins for ultrasonic sensors
  pinMode(trigLeft, OUTPUT);
  pinMode(echoLeft, INPUT);
  pinMode(trigCenter, OUTPUT);
  pinMode(echoCenter, INPUT);
  pinMode(trigRight, OUTPUT);
  pinMode(echoRight, INPUT);

  // Setup pins for the motor
  pinMode(motorPin1, OUTPUT);
  pinMode(motorPin2, OUTPUT);
  pinMode(enablePin, OUTPUT);
  pinMode(standbyPin, OUTPUT);
  pinMode(led, OUTPUT);

  digitalWrite(standbyPin, HIGH);  // Enable the motor

  // Servo setup
  servo.attach(pinServo);  // Attach the servo to the specified pin
  servo.write(angleCenter);  // Position the servo initially in the center

  // Read the distances from the ultrasonic sensors
  distanceLeft = measureDistance(trigLeft, echoLeft);
  distanceCenter = measureDistance(trigCenter, echoCenter);
  distanceRight = measureDistance(trigRight, echoRight);
  delay(100);  // Small delay between measurements

  // Print measured distances
  Serial.print("Distance Left: ");
  Serial.println(distanceLeft);
  Serial.print("Distance Center: ");
  Serial.println(distanceCenter);
  Serial.print("Distance Right: ");
  Serial.println(distanceRight);
  Serial.println("-----------Program started--------- ");
  
  // Initialize as I2C slave
  Wire.begin(SLAVE_ADDR);
  Wire.onReceive(receiveData);  // Set interrupt for receiving data
  Serial.println("Slave started.");

  // Determine the lane based on the distances
  if (distanceLeft < 70 && distanceCenter < 150) {
    lane = 3;
  } else if (distanceLeft < 50 && distanceCenter < 150) {
    lane = 2;
  } else if (distanceLeft < 30 && distanceCenter < 150) {
    lane = 1;
  }

  // Print the determined lane
  Serial.print("Lane: ");
  Serial.println(lane);
}

void loop() {
  // Update the distance measurements
  distanceLeft = measureDistance(trigLeft, echoLeft);
  distanceCenter = measureDistance(trigCenter, echoCenter);
  distanceRight = measureDistance(trigRight, echoRight);
  unsigned long currentTime = millis();  // Get the current time

  // Print measured distances
  Serial.print("Distance Left: ");
  Serial.print(distanceLeft);
  Serial.print(" cm, Distance Right: ");
  Serial.print(distanceRight);
  Serial.print(" cm, Distance Center: ");
  Serial.println(distanceCenter);

  // Lane and turn logic based on the distances
  if (distanceLeft < 150 && distanceCenter < 200 && distanceRight < 300) {
    servo.write(angleRight);  // Move the servo to the right
    delay(500);  // Small delay to stabilize the movement
    turnCount++;
    Serial.println("Turning right.");
  } else if (distanceLeft < 100) {
    servo.write(angleLeft);  // Move the servo to the left
    delay(500);  // Small delay to stabilize the movement
    turnCount++;
    Serial.println("Turning left.");
  } else if (distanceCenter < 100) {
    servo.write(angleCenter);  // Keep the servo in the center
    Serial.println("Moving straight.");
  }

  // Check if data has been received via I2C
  if (dataReceived) {
    // Execute the action corresponding to the detected signature and region
    executeAction(region, signature);
    delay(2000);  // Wait for a while before the next action
    dataReceived = false;  // Reset the data received flag
  }

  delay(100);  // Small delay before the next loop iteration
}

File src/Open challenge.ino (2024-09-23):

// Library for using the servo motor on the Arduino Nano ESP32
#include <ESP32Servo.h> // This library provides an interface to control servo motors with ESP32-based boards.

// The 3 ultrasonic sensors pin declaration
// Left ultrasonic sensor pins
const int trigIzquierdo = 11; // Trigger pin for the left ultrasonic sensor
const int echoIzquierdo = 12; // Echo pin for the left ultrasonic sensor

// Center ultrasonic sensor pins
const int trigCentro = 9; // Trigger pin for the center ultrasonic sensor
const int echoCentro = 10; // Echo pin for the center ultrasonic sensor

// Right ultrasonic sensor pins
const int trigDerecho = 7; // Trigger pin for the right ultrasonic sensor
const int echoDerecho = 8; // Echo pin for the right ultrasonic sensor

// LED pin (indicated with a question mark "quejesto???", possibly for debugging or signaling)
const int led = 13; // Pin connected to an LED, likely used to indicate a specific event or condition

// TB6612 motor driver pins
const int motorPin1 = 4; // Pin connected to IN1 of the TB6612 motor driver
const int motorPin2 = 5; // Pin connected to IN2 of the TB6612 motor driver
const int enablePin = 2; // PWM pin to control motor speed
const int standbyPin = 3; // STBY pin to activate/deactivate the motor driver

// Servo and its angles
Servo servoDireccion; // Declares the servo motor as "servoDireccion"
const int pinServo = 6; // Pin where the servo motor is connected
const int anguloIzquierda = 60; // Angle for turning the servo to the left
const int anguloCentro = 95; // Center angle of the servo (neutral position)
const int anguloDerecha = 130; // Angle for turning the servo to the right

// Variable to store the lane number, initialized to 0
int carril = 0; 

// Variable for detecting curves, initialized to 0
int curva = 0;

unsigned long tiempoUltimaAccion = 0; // Stores the time of the last action
const long bloqueoTiempo = 2000; // Time block for 2 seconds to avoid frequent actions

// Variables for storing the distances measured by each ultrasonic sensor
long distanciaIzquierdo;
long distanciaCentro;
long distanciaDerecho;

// Function to measure distance using an ultrasonic sensor
long medirDistancia(int trigPin, int echoPin) {
  // Send out a pulse
  digitalWrite(trigPin, LOW);
  delayMicroseconds(2);
  digitalWrite(trigPin, HIGH);
  delayMicroseconds(10);
  digitalWrite(trigPin, LOW);

  // Measure the duration of the echo pulse
  long duracion = pulseIn(echoPin, HIGH);
  
  // Convert the duration into distance (in centimeters)
  long distancia = duracion * 0.034 / 2; 

  return distancia;
}


// Function to make the motor move forward
void avanzar(int velocidad) {
  digitalWrite(motorPin1, HIGH); // Set IN1 to high
  digitalWrite(motorPin2, LOW);  // Set IN2 to low
  analogWrite(enablePin, velocidad); // Apply the speed using PWM
}

// Function to stop the motor
void detenerMotor() {
  digitalWrite(motorPin1, LOW); // Set both IN1 and IN2 to low to stop the motor
  digitalWrite(motorPin2, LOW);
  analogWrite(enablePin, 0); // Stop the PWM signal
}

// Function executed once at the beginning
void setup() {
  // Initialize serial communication at a baud rate of 9600
  Serial.begin(9600);
  delay(500); // Short delay to ensure serial communication is ready

  // Set the pins for the ultrasonic sensors
  pinMode(trigIzquierdo, OUTPUT);
  pinMode(echoIzquierdo, INPUT);
  pinMode(trigCentro, OUTPUT);
  pinMode(echoCentro, INPUT);
  pinMode(trigDerecho, OUTPUT);
  pinMode(echoDerecho, INPUT);

  // Set the motor and standby pins
  pinMode(motorPin1, OUTPUT);
  pinMode(motorPin2, OUTPUT);
  pinMode(enablePin, OUTPUT);
  pinMode(standbyPin, OUTPUT);
  pinMode(led, OUTPUT); // Set the LED pin

  // Activate the motor driver (take it out of standby mode)
  digitalWrite(standbyPin, HIGH);

  // Attach and initialize the servo motor
  servoDireccion.attach(pinServo);
  servoDireccion.write(anguloCentro); // Start the servo in the center position

  // Measure distances from all ultrasonic sensors
  distanciaIzquierdo = medirDistancia(trigIzquierdo, echoIzquierdo);
  distanciaCentro = medirDistancia(trigCentro, echoCentro);
  distanciaDerecho = medirDistancia(trigDerecho, echoDerecho);
  delay(100); // Small delay

  // Print out the measured distances for debugging
  Serial.print("Distancia Izquierdo: ");
  Serial.println(distanciaIzquierdo);
  Serial.print("Distancia Centro: ");
  Serial.println(distanciaCentro);
  Serial.print("Distancia Derecho: ");
  Serial.println(distanciaDerecho);

  // Check distances to determine the lane based on sensor readings
  if (distanciaIzquierdo < 70 && distanciaCentro < 150) {
    carril = 3; // Set lane to 3 if both left and center distances meet the condition
    digitalWrite(led, HIGH); // Turn on the LED
  }
  if (distanciaIzquierdo < 50 && distanciaCentro < 150) {
    carril = 2; // Set lane to 2 if left distance is smaller
    digitalWrite(led, HIGH); // Turn on the LED
  }
  if (distanciaIzquierdo < 30 && distanciaCentro < 150) {
    carril = 1; // Set lane to 1 if left distance is even smaller
    digitalWrite(led, HIGH); // Turn on the LED
  }

  // Print the current lane number
  Serial.print("Carril: ");
  Serial.println(carril); // Print the lane value with a line break
}
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

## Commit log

2024-07-15 Create 3d prints
2024-09-18 Rename PixyCam2 case (1).stl to PixyCam v2 case.stl
    [PixyCam v2 case.stl]
2024-09-25 Rename Agregar un título.pdf to CIRCUIT DIAGRAM.pdf
2024-10-17 Create Steering
2024-11-13 Create Obstacle ChallengeLatest.ino
    Our newest version of the code for the obstcacle challenge, you can see we dropped the two arduinos system and now we use a single arduino, the a00005 on the prototype.
2024-11-13 Rename LEFT.jpg to Internaional First Prototype.jpg
2024-11-15 Update Obstacle Challenge Latest.ino
    adding the PD to the code to avoid the walls during the obstacle challenge, hope it works lets give it a try
    [Obstacle Challenge Latest.ino]
2024-11-20 Circuit diagram Terrenator
2024-11-20 TERRENATOR´S CIRCUIT DIAGRAM
2024-11-20 Circuit diagram README.md
